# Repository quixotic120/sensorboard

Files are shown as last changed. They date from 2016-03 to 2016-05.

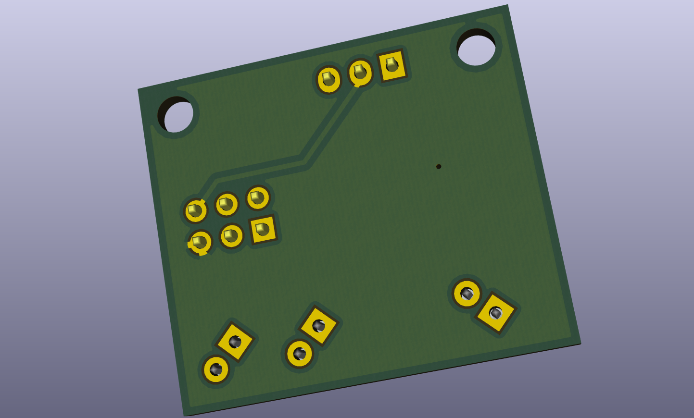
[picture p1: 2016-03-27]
MiniDifIR/diffIR_rear.png

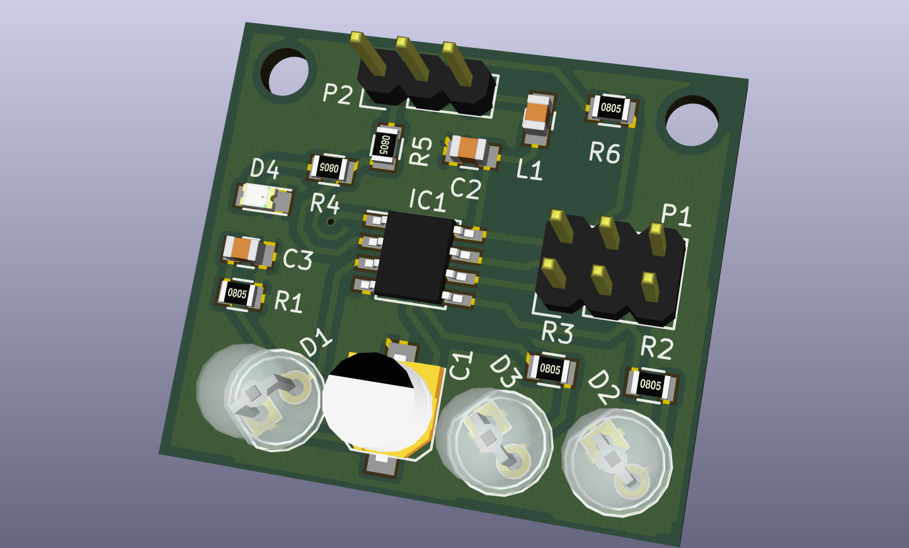
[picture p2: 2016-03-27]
MiniDifIR/diffIR_front.png

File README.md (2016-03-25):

Sense board - my layout (which is very close to orig tbh), orig by dc42 - his readme below. cc4.0-noncommercial license

OrmerodSensorBoard
==================

Here are the design files for my Z-height sensor board add-on to the RepRapPro Ormerod 3D printer. This board replaces the original IR sensor board used for Z-probing. It has the following advantages over the original:

1. It uses modulated infrared light, which makes it much less sensitive to ambient infrared such as is found in sunlight and in incandescent artificial light.
2. The sensor board is mounted on the hot end so that the sensor head is in-line with the nozzle in the x-direction. This makes it much less sensitive to variations in head sag.
3. The board includes the facility to mount the hot end connectors, eliminating the need for the original 6-pin connector. The new connectors are more reliable and more easily disassembled. In particular, the crimp receptacles can more easily be removed from the connector shell.
4. The board can accommodate three Cree LEDs to direct light on the work being printed. Alternatively, it can provide 12V power to an LED strip, or a constant-current supply to external LEDs.
5. The board includes provision for thermostatic control of the hot end fan. The fan is turned on when the hot end temperature exceeds approximately 42C, or when the board detects a hot end temperature measurement fault.
6. The board can also support an experimental ultrasonic sensor. This allows z-probing to be done anywhere on the bed. Due to variation in the speed of sound with temperature, the ultrasonic sensor is a little temperature-sensitive, but this can be compensated in the firmware.

Work is in progress to adapt the board for capacitive height sensing.

For assembly and usage instructions, please visit: http://miscsolutions.wordpress.com/assembling-and-using-the-eschertech-ormerod-hot-end-board/

I supply bare boards, kits of parts with all SMD components ready-mounted, and fully assembled boards. Contact me via the RepRap Ormerod forum at http://forums.reprap.org/list.php?340 by sending a personal message to dc42.

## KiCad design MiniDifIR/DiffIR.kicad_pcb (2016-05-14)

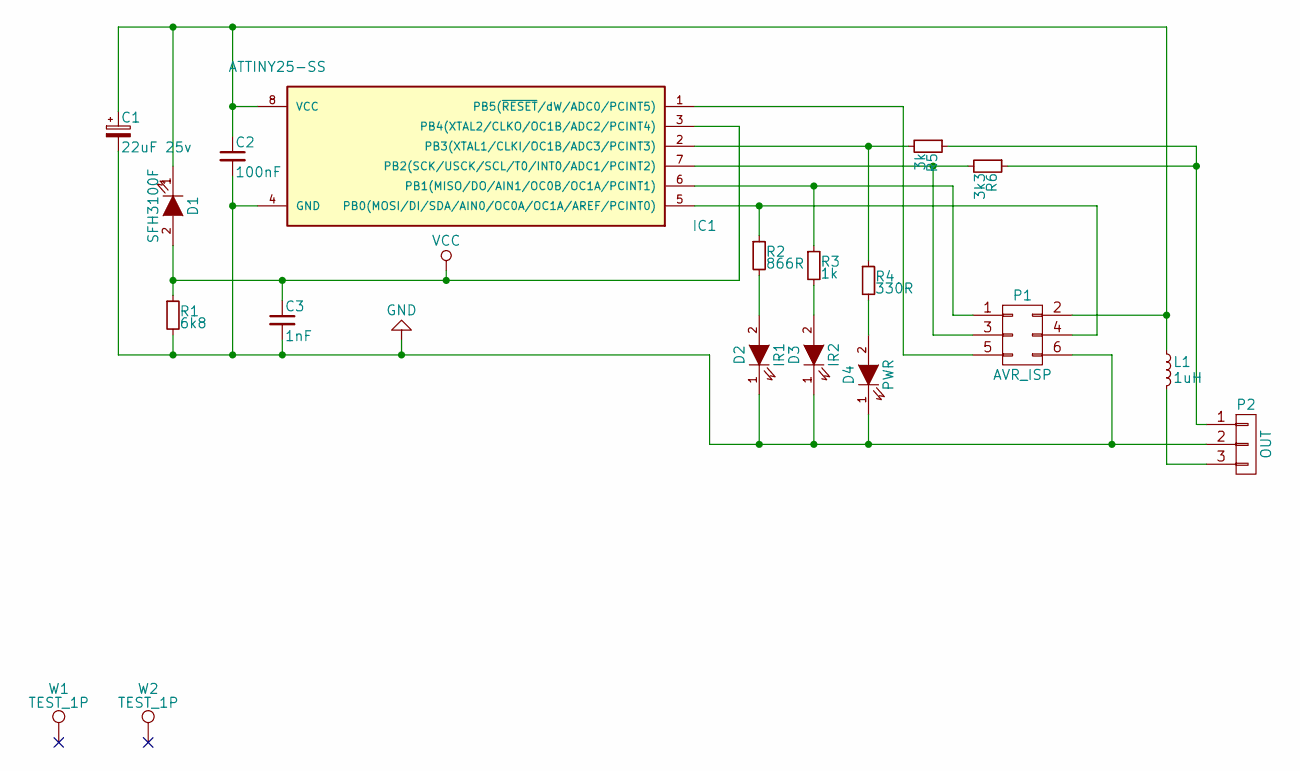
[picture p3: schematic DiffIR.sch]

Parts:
C1: 22uF 25v; c_elec_5x5.7
C2: 100nF; C_0805
C3: 1nF; C_0805
D1: SFH3100F; LED-5MM
D2: IR1; LED-5MM
D3: IR2; LED-5MM
D4: PWR; LED_0805
IC1: ATTINY25-SS; SOIC-8_3.9x4.9mm_Pitch1.27mm
L1: 1uH; C_0805
P1: AVR_ISP; Pin_Header_Straight_2x03
P2: OUT; Pin_Header_Straight_1x03
R1: 6k8; R_0805
R2: 866R; R_0805
R3: 1k; R_0805
R4: 330R; R_0805
R5: 3k; R_0805
R6: 3k3; R_0805
W1, W2: TEST_1P; MountingHole_3mm

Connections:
GND: C1.2, C2.2, C3.2, D2.1 (K), D3.1 (K), D4.1 (K), IC1.4 (GND), P1.6, P2.2, R1.2
unnamed: C1.1, C2.1, D1.1 (K), IC1.8 (VCC), L1.1, P1.2
unnamed: D2.2 (A), R2.2
unnamed: D3.2 (A), R3.2
unnamed: D4.2 (A), R4.2
unnamed: IC1.1 (PB5(~RESET~/dW/ADC0/PCINT5)), P1.5
unnamed: IC1.2 (PB3(XTAL1/CLKI/OC1B/ADC3/PCINT3)), R4.1, R5.2
unnamed: IC1.5 (PB0(MOSI/DI/SDA/AIN0/OC0A/OC1A/AREF/PCI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), P1.4, R2.1
unnamed: IC1.6 (PB1(MISO/DO/AIN1/OC0B/OC1A/PCINT1)), P1.1, R3.1
unnamed: IC1.7 (PB2(SCK/USCK/SCL/T0/INT0/ADC1/PCINT2)), P1.3, R6.2
unnamed: L1.2, P2.3
unnamed: P2.1, R5.1, R6.1
VCC: C3.1, D1.2 (A), IC1.3 (PB4(XTAL2/CLKO/OC1B/ADC2/PCINT4)), R1.1

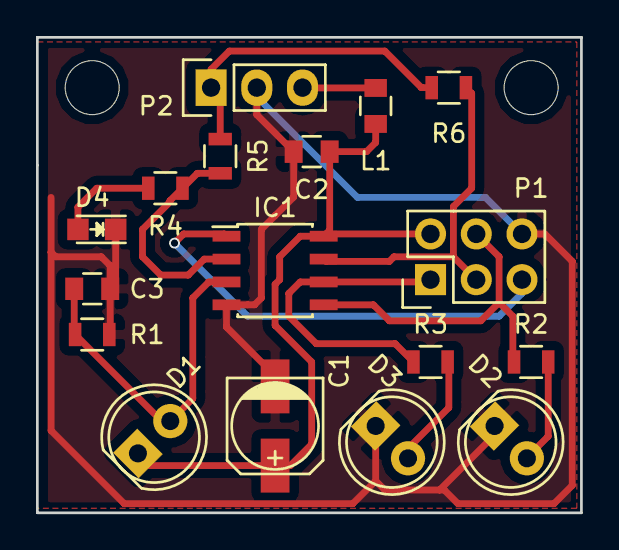
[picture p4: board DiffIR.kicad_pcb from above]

Board: 2 copper layers, 30.2 x 26.4 mm, 19 parts (0 on the bottom side), 13 nets.

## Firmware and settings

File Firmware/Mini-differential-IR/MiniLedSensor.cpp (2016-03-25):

/*
 * MiniLedSensor.cpp
 *
 * Created: 03/05/2015 11:06:12
 *  Author: David Crocker, Escher Technologies Ltd.
 * Licensed under the GNU General Public License version 3. See http://www.gnu.org/licenses/gpl-3.0.en.html.
 * This software is supplied WITHOUT WARRANTY except when it is supplied pre-programmed into
 * an electronic device that was manufactured by or for Escher Technologies Limited.
 */ 

// Version 3: changed modulation scheme to allow for charging/discharging of phototransistor base-collector capacitance
// Version 4: increased maximum value of the pullup resistor we look for to 150K, because it is higher on the Arduino Due
// Version 5: increased maximum value of the pullup resistor we look for to 160K, to get reliable results with the 150K resistor in the test rig
// Version 6: Don't enable pullup resistor on phototransistor input

#include "ecv.h"

#ifdef __ECV__
#define __attribute__(_x)
#define __volatile__
#endif

#ifdef __ECV__
#pragma ECV noverifyincludefiles
#endif

#include <avr/io.h>
#include <avr/interrupt.h>
#include <avr/eeprom.h>
#include <avr/wdt.h>

#ifdef __ECV__
#pragma ECV verifyincludefiles
#undef cli
#undef sei
extern void cli();
extern void sei();
#endif

#define ISR_DEBUG	(0)		// set nonzero to use PB2 as debug output pin

#define BITVAL(_x) static_cast<uint8_t>(1u << (_x))

// Pin assignments:
// PB0/MOSI			far LED drive, active high
// PB1/MISO			near LED drive, active high
// PB2/ADC1/SCK		output to Duet via 12K resistor
// PB3/ADC3			output to Duet via 10K resistor
// PB4/ADC2			input from phototransistor
// PB5/ADC0/RESET	not available, used for programming

#ifndef __ECV__
__fuse_t __fuse __attribute__((section (".fuse"))) = {0xE2u, 0xDFu, 0xFFu};
#endif

const unsigned int AdcPhototransistorChan = 2;				// ADC channel for the phototransistor
const unsigned int AdcPortBDuet10KOutputChan = 3;			// ADC channel for the 10K output bit, when we use it as an input
const unsigned int PortBNearLedBit = 1;
const unsigned int PortBFarLedBit = 0;
const unsigned int PortBDuet10KOutputBit = 3;
const unsigned int PortBDuet12KOutputBit = 2;

const uint8_t PortBUnusedBitMask = 0;

// Approximate MPU frequency (8MHz internal oscillator)
const uint32_t F_CPU = 8000000uL;

// IR parameters. These also allow us to receive a signal through the command input.
const uint16_t interruptFreq = 8000;						// interrupt frequency. We run the IR sensor at one quarter of this, i.e. 2kHz
															// highest usable value is about 9.25kHz because the ADC needs 13.5 clock cycles per conversion.
const uint16_t divisorIR = (uint16_t)(F_CPU/interruptFreq);
const uint16_t prescalerIR = 8;								// needs to be high enough to get baseTopIR below 256
const uint16_t baseTopIR = (divisorIR/prescalerIR) - 1u;
const uint16_t cyclesAveragedIR = 8;						// must be a power of 2, max 64 (unless we make onSumIR and offSumIR uint32_t)
															// *** max is now 16 because we add the 3 sums when we sense the pullup resistor ***

const uint16_t farThreshold = 10u * cyclesAveragedIR;		// minimum far reading for us to think the sensor is working properly
const uint16_t saturatedThreshold = 870u * cyclesAveragedIR; // minimum reading for which we consider the sensor saturated

const uint16_t kickFreq = 16;
const uint16_t kickIntervalTicks = interruptFreq/kickFreq;

// IR variables
typedef uint8_t invariant(value < cyclesAveragedIR) irIndex_t;

struct IrData
{
	uint16_t readings[cyclesAveragedIR];
	volatile uint16_t sum;
	irIndex_t index;

	void addReading(uint16_t arg)
	writes(*this; volatile)
	pre(invar())
	pre(arg <= 1023)
	post(invar())
	{
		sum = sum - readings[index] + arg;
		readings[index] = arg;
		index = static_cast<irIndex_t>((index + 1u) % cyclesAveragedIR);
	}
	
	void init()
	writes(*this; volatile)
	post(invar());

	ghost(
		bool invar() const
			returns((forall r in readings :- r <= 1023) && sum == + over readings);
	)
	
#ifdef __ECV__
	// Dummy constructor to keep eCv happy
	IrData() : index(0) {}
#endif
};

IrData nearData, farData, offData;
	
// General variables
volatile uint16_t tickCounter = 0;					// counts system ticks, lower 2 bits also used for ADC/LED state
uint16_t lastKickTicks = 0;							// when we last kicked the watchdog
bool digitalOutput = false;
bool running = false;


// ISR for the timer 0 compare match A interrupt
// This works on a cycle of 4 readings as follows:
// far led on, near led on, leds off, null
#ifdef __ECV__
void TIM0_COMPB_vect()
#else
ISR(TIM0_COMPB_vect)
#endif
writes(nearData; farData; offData)
writes(volatile)
pre(nearData.invar(); farData.invar(); offData.invar())
post(nearData.invar(); farData.invar(); offData.invar())
{
	uint16_t adcVal = ADC & 1023u;					// get the ADC reading from the previous conversion
	uint8_t locTickCounter = (uint8_t)tickCounter;
	while (TCNT0 < 3u * 8u) {}						// delay a little until the ADC s/h has taken effect. 3 ADC clocks should be enough, and 1 ADC clock is 8 timer 0 clocks.
	switch(locTickCounter & 0x03u)
	{
		case 0:
			// Far LED is on, we just did no reading, we are doing a far reading now and an off reading next
			PORTB &= ~BITVAL(PortBFarLedBit);		// turn far LED off
			break;
		
		case 1:
			// LEDs are off, we just did a far reading, we are doing a off reading now and a near reading next			
			if (running)
			{
				farData.addReading(adcVal);
			}
			PORTB |= BITVAL(PortBNearLedBit);		// turn near LED on
			break;
					
		case 2:
			// Near LED is on, we just did an off reading, we are doing a near reading now and a dummy off reading next
			if (running)
			{
				offData.addReading(adcVal);
			}
			PORTB &= ~BITVAL(PortBNearLedBit);		// turn near LED off
			break;

		case 3:
			// Far LED is on, we just did an off reading, we are doing another off reading now which will be discarded
			if (running)
			{
				nearData.addReading(adcVal);
			}
			PORTB |= BITVAL(PortBFarLedBit);		// turn far LED on
			break;
	}
	++tickCounter;
}

#if 0	// unused at present

// Delay for a little while
// Each iteration of the loop takes 4 clocks plus one clock per NOP instruction in the body.
// The additional overhead for the function, including calling it, is 12 clocks.
// Therefore, with F_CPU = 8MHz and using 4 NOP instructions, it delays n + 1.5 microseconds.
void shortDelay(uint8_t n)
{
	for (uint8_t i = 0; i < n; ++i)
	keep(i <= n)
	decrease(n - i)
	{
#ifndef __ECV__			// eCv doesn't understand asm
		asm volatile ("nop");
		asm volatile ("nop");
		asm volatile ("nop");
		asm volatile ("nop");
#endif
	}
}

#endif

// Give a G31 reading of about 0
inline void SetOutputOff()
writes(volatile)
{
	// We do this in 2 operations, each of which is atomic, so that we don't mess up what the ISR is doing with the LEDs.
	PORTB &= ~BITVAL(PortBDuet10KOutputBit);
	PORTB &= ~BITVAL(PortBDuet12KOutputBit);
}

// Give a G31 reading of about 445 indicating we are approaching the trigger point
inline void SetOutputApproaching()
writes(volatile)
{
	// We do this in 2 operations, each of which is atomic, so that we don't mess up what the ISR is doing with the LEDs.
	PORTB &= ~BITVAL(PortBDuet10KOutputBit);
	PORTB |= BITVAL(PortBDuet12KOutputBit);
}	

// Give a G31 reading of about 578 indicating we are at/past the trigger point
inline void SetOutputOn()
writes(volatile)
{
	// We do this in 2 operations, each of which is atomic, so that we don't mess up what the ISR is doing with the LEDs.
	PORTB |= BITVAL(PortBDuet10KOutputBit);
	PORTB &= ~BITVAL(PortBDuet12KOutputBit);
}

// Give a G31 reading of about 1023 indicating that the sensor is saturating
inline void SetOutputSaturated()
writes(volatile)
{
	// We do this in 2 operations, each of which is atomic, so that we don't mess up what the ISR is doing with the LEDs.
	PORTB |= BITVAL(PortBDuet10KOutputBit);
	PORTB |= BITVAL(PortBDuet12KOutputBit);
}

// Get the tick counter from outside the ISR. As it's more than 8 bits long, we need to disable interrupts while fetching it.
inline uint16_t GetTicks()
writes(volatile)
{
	cli();
	uint16_t ticks = tickCounter;
	sei();
	return ticks;
}

// Check whether we need to kick the watchdog
void CheckWatchdog()
writes(lastKickTicks; volatile)
{
	if (GetTicks() - lastKickTicks >= kickIntervalTicks)
	{
#ifndef __ECV__
		wdt_reset();											// kick the watchdog
#endif
		lastKickTicks += kickIntervalTicks;
	}
}

// Delay for a specified number of ticks
void DelayTicks(uint16_t ticks)
writes(lastKickTicks; volatile)
{
	uint16_t startTicks = GetTicks();
	for (;;)
	{
		CheckWatchdog();
		if (GetTicks() - startTicks >= ticks)
		{
			break;
		}
	}
}

// Run the IR sensor and the fan
void runIRsensor()
writes(running; nearData; farData; offData; lastKickTicks; digitalOutput; volatile)
{
	running = false;
	nearData.init();
	farData.init();
	offData.init();

	cli();
	// Set up timer 1 in mode 2 (CTC mode)
	GTCCR = 0;
	TCCR0A = BITVAL(WGM01);									// no direct outputs, mode 2
	TCCR0B = 0;												// set the mode, clock stopped for now
	TCNT0 = 0;
	OCR0A = baseTopIR;
	OCR0B = 0;
	TIFR = BITVAL(OCF0B);									// clear any pending interrupt
	TIMSK = BITVAL(OCIE0B);									// enable the timer 0 compare match B interrupt
	TCCR0B |= BITVAL(CS01);									// start the clock, prescaler = 8
	
	ADMUX = (uint8_t)AdcPortBDuet10KOutputChan;				// select the 10K resistor output bit, single ended mode
	ADCSRA = BITVAL(ADEN) | BITVAL(ADPS2) | BITVAL(ADATE) | BITVAL(ADPS1);	// enable ADC, auto trigger enable, prescaler = 64 (ADC clock ~= 125kHz)
	ADCSRB = BITVAL(ADTS2) | BITVAL(ADTS0);					// start conversion on timer 0 compare match B, unipolar input mode
	tickCounter = 0;
	lastKickTicks = 0;
	sei();
	
	// Determine whether to provide a digital output or a 4-state output.
	// We do this by checking to see whether the connected electronics provided a pullup resistor on the output.
	// If a pullup resistor is detected, we provide a digital output, else we provide an analog output.
	// Wait a while before we do this test, so that Duet firmware has a chance to turn the internal pullup (50K to 150K) off,
	// and Arduino/RAMPS firmware has a chance to turn the internal pullup (20K to 50K) on.
	SetOutputOff();
	DDRB &= ~BITVAL(PortBDuet10KOutputBit);					// set the pin to an input, pullup disabled because output is off
	
	// Wait 4 seconds, keeping the watchdog happy
	DelayTicks(4u);											// ignore the readings from the first few interrupts after changing mode
	running = true;											// start collecting readings
	DelayTicks(4u * interruptFreq);							// give the printer electronics time to enable/disable its pullup resistor
	running = false;										// stop collecting readings
	
	// Readings have been collected into all three of nearData, farData, and offData.
	// We are looking for a pullup resistor of no more than 75K on the output to indicate that we should use a digital output.
	// DC 2014-08-04 we now look for no more than 160K, because on the Arduino Due the pullups are in the range 50K-150K.
	digitalOutput = offData.sum + nearData.sum + farData.sum >= (3600UL * cyclesAveragedIR * 1024UL * 3u)/(160000UL + 3600UL);
	
	// Change back to normal operation mode
	ADMUX = (uint8_t)AdcPhototransistorChan;				// select input 1 = phototransistor, single ended mode
	DDRB |= BITVAL(PortBDuet10KOutputBit);					// set the pin back to being an output

	// Flash the LED twice if we are providing a digital output, four times if we are providing an analog output
	for (uint8_t flashesToGo = (digitalOutput) ? 2u : 4u; flashesToGo != 0u; )
	{
		SetOutputSaturated();								// turn LED on
		DelayTicks(interruptFreq/4u);
		SetOutputOff();
		DelayTicks(interruptFreq/4u);
		--flashesToGo;
	}
	
	// Clear out the data and start collecting data from the phototransistor
	nearData.init();
	farData.init();
	offData.init();

	running = true;											// tell interrupt handler to collect readings
	DelayTicks(4u * cyclesAveragedIR);						// wait until we have a full set of readings

	// Start normal operation
	for (;;)
	keep(nearData.invar(); farData.invar(); offData.invar())
	{
		cli();
		uint16_t locNearSum = nearData.sum;
		uint16_t locFarSum = farData.sum;
		uint16_t locOffSum = offData.sum;
		sei();
			
		if (locNearSum >= saturatedThreshold || locFarSum >= saturatedThreshold)
		{
			SetOutputSaturated();							// sensor is saturating, so set the output full on to indicate this
		}
		else
		{
			locNearSum = (locNearSum > locOffSum) ? locNearSum - locOffSum : 0;
			locFarSum = (locFarSum > locOffSum) ? locFarSum - locOffSum : 0;
			
			// Differential modulated IR sensor mode								
			if (locFarSum >= farThreshold && locNearSum > locFarSum)
			{
				if (digitalOutput)
				{
					SetOutputSaturated();
				}
				else
				{
					SetOutputOn();					
				}
			}
			else if (!digitalOutput && locFarSum >= farThreshold && locNearSum * 6UL >= locFarSum * 5UL)
			{
				SetOutputApproaching();
			}
			else
			{
				SetOutputOff();
			}
		}

		CheckWatchdog();	
	}
}


// Main program
int main(void)
writes(volatile)
writes(running; digitalOutput)
writes(nearData; farData; offData)	// IR variables
writes(lastKickTicks)
{
	cli();
	DIDR0 = BITVAL(AdcPhototransistorChan);					// disable digital input buffers on ADC pins

	// Set ports and pullup resistors
	PORTB = PortBUnusedBitMask;								// enable pullup on unused I/O pins
	
	// Enable outputs
	DDRB = BITVAL(PortBNearLedBit) | BITVAL(PortBFarLedBit) | BITVAL(PortBDuet10KOutputBit) | BITVAL(PortBDuet12KOutputBit);
	
	sei();

#ifndef __ECV__												// eCv++ doesn't understand gcc assembler syntax
	wdt_enable(WDTO_500MS);									// enable the watchdog (we kick it when checking the fan)	
#endif
		
	runIRsensor();											// doesn't return
	return 0;												// to keep gcc happy
}

// Initialize the IR data structure
void IrData::init()
{
	for (uint8_t i = 0; i < cyclesAveragedIR; ++i)
	writes(i; *this; volatile)
	keep(i <= cyclesAveragedIR)
	keep(forall j in 0..(i-1) :- readings[j] == 0)
	decrease(cyclesAveragedIR - i)
	{
		readings[i] = 0;
	}
	index = 0;
	sum = 0;
}

// End

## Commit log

2016-03-25 dc42 diff optostop
    remix of dc42’s differential IR endstop
    [DiffIR.kicad_pcb, DiffIR.sch]
2016-03-27 thickened traces
    [DiffIR.kicad_pcb, DiffIR.kicad_pcb_narrow.kicad_pcb, DiffIR.sch]
2016-05-14 diff IR
    [DiffIR.kicad_pcb]
